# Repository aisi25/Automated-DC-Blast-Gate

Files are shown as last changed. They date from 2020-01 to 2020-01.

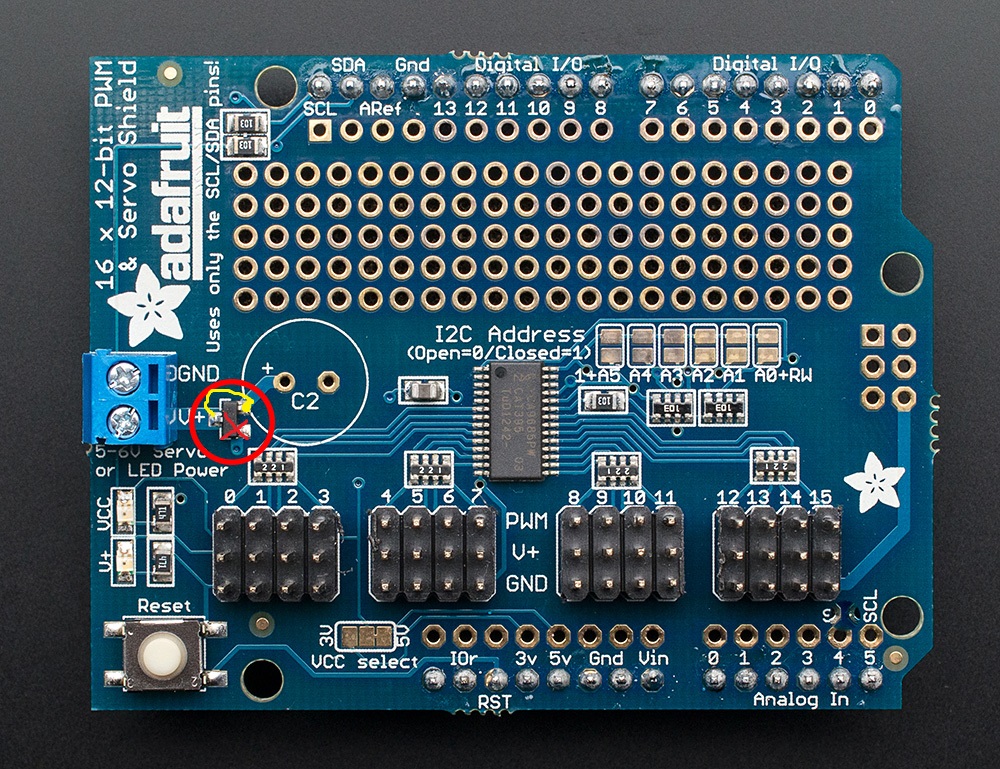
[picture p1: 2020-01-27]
Sheild Fix.jpg

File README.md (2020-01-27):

I hired a professional several months ago to write this Arduino code to turn on/off dust collection system and open/close its blast gates
with Servos via a push buttons mounted on each tool in my workshop.

Before implementing this system I used to control the DC wirelessly with "PSI Woodworking LR2244 Long Ranger" and manually open/close the blast gates, and now the Arduino is using the same wireless controller to control the DC system and open/close the blast gates using servos mounted on each one with 3D printed parts (attached) .

I used Servo Shield powered by separate 8A power supply for the Servos, and I used CAT 5e network cable to wire the push buttons and the Servos to the Arduino.

In the beginning of using the system the servo driver/shield MOSFET burnt out when I connect all the servos because its not designed for continuous power for more than 3 parallel servos, and the solution was to bypass it. (attached)

And also there was an issue where the some servos will become warm and draw current when idle because the power is constantly provided to them and the Arduino trying keep each gate at the exact set angle while that is difficult to be done in such application, and this has been fixed by adding a relay to disconnect the power to the Shield after executing the command.

The 3D printed servo mount has a place for a micro limit switch wired to green & red LEDs to indicate the gate status physically

Main Parts:

Arduino UNO R3

SunFounder PCA9685 16 Channel 12 Bit PWM Servo Driver

DS3218 servo 20KG Full Metal Gear 25T Servo

25T Servo Horn

Momentary Hinge Roller Lever Micro Limit Mini Switch (https://www.amazon.com/gp/product/B06XFL4MZ2/ref=ppx_yo_dt_b_search_asin_title?ie=UTF8&psc=1)

4in Self-Cleaning Metal Blast Gate

PSI Woodworking LR2244 Long Ranger

Thank You.

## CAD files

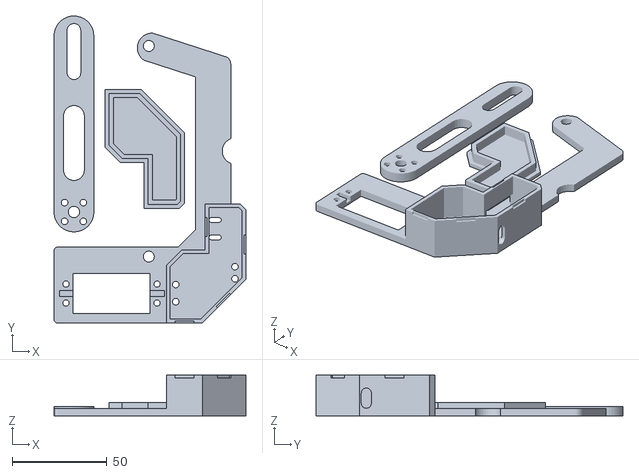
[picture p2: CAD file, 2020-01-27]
Blast Gate.stl
101.2 x 161.8 x 21.5

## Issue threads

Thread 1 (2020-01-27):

Suddenly Close All Trigger

aisi25, 2020-01-27:
I've been using the system lightly with no major issues for the mentioned period,
but lately I was turning the system for each tool for more than approximately 3-5 min and suddenly the Arduino will trigger Close All while the Dust Collection motor still running, and sometimes I can re-open the tool blast gate with the button but other times there will be no response from the arduino until I restart it,  so far this happens while using my table saw and jointer/planner because they usually need to be on for longer than other tools for the projects I'm doing.

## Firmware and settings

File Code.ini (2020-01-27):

#define SIM 0 //Keep it 0
#define TEST_MODE 1  //To disable testing set it to 0
#define TOTAL_GATES 8
#define RELAY_1_PIN A0  //Channel 1 connection
#define RELAY_2_PIN A1  //Channel 2 connection
const int PUSH_BUTTON_PINS[TOTAL_GATES] = {2, 3, 4, 5, 6, 7, 8, 9};
#define GATE_CLOSE_WAIT 5000 //milliseconds
#define CLOSE_ALL_BTN_PIN A2
#define OPEN_ALL_BTN_PIN A3
#define POWER_RELAY_PIN 10


const int gateMinMax_pwm[TOTAL_GATES][2] = {  //(out of 4096)
  /*open, close*/
  {250, 415}, //Gate 1
  {230, 405}, //Gate 2
  {230, 405}, //Gate 3
  {285, 425}, //Gate 4
  {250, 405}, //Gate 5
  {250, 415}, //Gate 6
  {250, 405}, //Gate 7
  {250, 415}, //Gate 8
};

const int gateOpenClose_angle[TOTAL_GATES][2] = {  //0 to 180, you can also put inverse angles i.e (180, 0)
  /*close, open*/
  {0, 180}, //Gate 1
  {0, 180}, //Gate 2
  {0, 180}, //Gate 3
  {0, 180}, //Gate 4
  {0, 180}, //Gate 5
  {0, 180}, //Gate 6
  {0, 180}, //Gate 7
  {0, 180}, //Gate 8
};

const int LED_red_green[TOTAL_GATES][2] = {  //pin numbers for red and green LEDs for each gate
  /*red, green*/
  {11, 12}, //Gate 1
  {11, 13}, //Gate 2
  {11, 12}, //Gate 3
  {11, 13}, //Gate 4
  {11, 12}, //Gate 5
  {11, 13}, //Gate 6
  {11, 12}, //Gate 7
  {11, 13}, //Gate 8
};



#include <Wire.h>
#if !SIM
#include <Adafruit_PWMServoDriver.h>
Adafruit_PWMServoDriver pwm = Adafruit_PWMServoDriver();
#else
#include <Servo.h>
Servo servos;
#endif

// Depending on your servo make, the pulse width min and max may vary, you
// want these to be as small/large as possible without hitting the hard stop
// for max range. You'll have to tweak them as necessary to match the servos you
// have!
#define OPEN_GATE 1
#define CLOSE_GATE 0

boolean btn_states[TOTAL_GATES];
boolean gate_states[TOTAL_GATES];
boolean close_all_btn = 0;
boolean open_all_btn = 0;
boolean motor_state = LOW;
unsigned long power_relay_timer = 0;
boolean power_relay_state = LOW;

void setup()
{
  pinMode(POWER_RELAY_PIN, OUTPUT);
  digitalWrite(POWER_RELAY_PIN, power_relay_state);
  Serial.begin(9600);
  Serial.println(F("Start"));
  for (int i = 0; i < TOTAL_GATES; i++)
  {
    gate_states[i] = CLOSE_GATE;
    btn_states[i] = 0;
    pinMode(PUSH_BUTTON_PINS[i], INPUT_PULLUP);
    pinMode(LED_red_green[i][0], OUTPUT);
    pinMode(LED_red_green[i][1], OUTPUT);
    digitalWrite(LED_red_green[i][0], HIGH);
    digitalWrite(LED_red_green[i][1], LOW);
  }
  pinMode(CLOSE_ALL_BTN_PIN, INPUT_PULLUP);
  pinMode(OPEN_ALL_BTN_PIN, INPUT_PULLUP);
  pinMode(RELAY_1_PIN, OUTPUT);
  pinMode(RELAY_2_PIN, OUTPUT);
  idle_pump();

  power_relay_state = HIGH;
  digitalWrite(POWER_RELAY_PIN, power_relay_state);
  delay(10);
  init_servos();

  delay(10);

#if TEST_MODE
  Serial.println(F("This is TEST_MODE"));
  Serial.println(F("ON Relay 1"));
  digitalWrite(RELAY_1_PIN, HIGH);
  delay(2000);
  Serial.println(F("OFF Relay 1"));
  digitalWrite(RELAY_1_PIN, LOW);
  delay(500);

  Serial.println(F("ON Relay 2"));
  digitalWrite(RELAY_2_PIN, HIGH);
  delay(2000);
  Serial.println(F("OFF Relay 2"));
  digitalWrite(RELAY_2_PIN, LOW);
  delay(1000);


  Serial.println(F("Opening all gates"));
  for (int i = 0; i < TOTAL_GATES; i++)
  {
    move_Gate(i, OPEN_GATE);
  }
  delay(2000);

  Serial.println("TESTING END");
#endif

  Serial.println(F("Closing all gates"));
  for (int i = 0; i < TOTAL_GATES; i++)
  {
    move_Gate(i, CLOSE_GATE);
  }
  delay(10);

  Serial.println(check_button_push(2));
  Serial.println(F("Press any button"));
}

unsigned long timerx = 0;
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

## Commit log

2020-01-27 The Wiring
    This wiring before adding the relay to disconnect the shield.
2020-01-27 Servo Driver Fix
2020-01-27 Servo Mount for 4" Self-Cleaning Metal Blast Gates
    Please confirm the fit for your blast gate
    [Blast Gate.stl]
